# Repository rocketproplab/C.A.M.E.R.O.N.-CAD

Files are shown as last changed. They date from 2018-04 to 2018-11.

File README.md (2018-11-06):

# C.A.M.E.R.O.N

The main PCB on Launchy that is responsible for all the Avionics tasks of the rocket

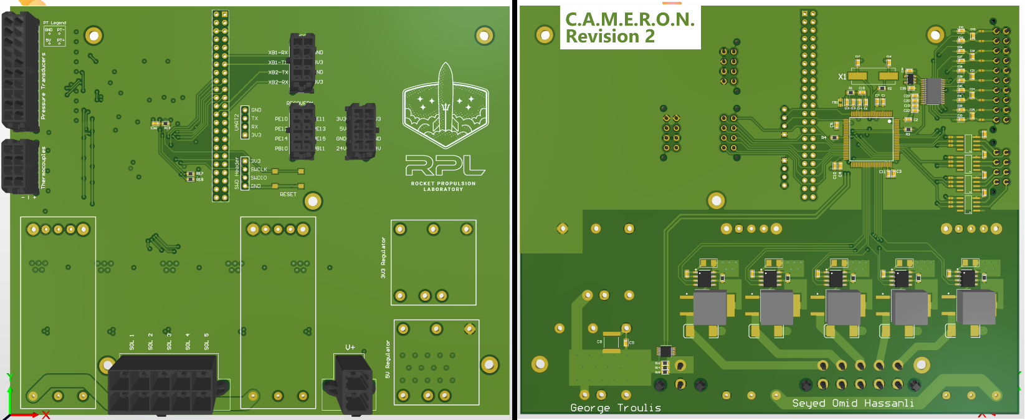
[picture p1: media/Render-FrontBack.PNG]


## Maintainer
CAMERON is maintained by George Troulis, with numerous contributions from Seyed Omid Hassanli

## Naming
C.A.M.E.R.O.N. stands for Changes All Mechanical and Electrical Requirements Over Night. It also happens to be the name of our beloved Chief Engineer, who has done a fantastic job at running RPL and assigning tasks and deadlines to everyone.

## Features

CAMERON contains the following features:
* Up to 36V input with 24V, 5V, and 3.3V rails
* Active current-monitoring IC connected to battery input
* BeagleBone Black (Flight Computer)
* Connector for 2 UARTs that connect the FC with XBee Radios
* STM32F4 "RIO" to interface with sensors
* Breakouts for Solenoids, Pressure Transducers, and Thermocouples
* SWD and UART Headers for debugging/programming the STM32F4
* Breakout for separate Recovery PCB that triggers chute at apogee

## Todo List for upcoming revisions
- [ ] Add indicator LEDs for various items
- [ ] Add designators to all components
- [ ] Shorten designators for multi-channel elements
- [X] Add Logo and Revision notes on the PCB
- [X] Fix footprint for solder bridge
- [X] Expand the diameter of the holes for the BeagleBone
- [X] Make annular rings for Molex connectors larger
- [X] FIX THE MOSFET FOOTPRINT (Gate and Drain are flipped)
- [X] Add thermal relief to pads
- [X] Add silk to the XBee connector and remove the J8 designator
- [X] FLIP BOOT PINS (test them first)
- [X] Move the "5V Regulator" Label away from the stitching vias
- [X] Add tenting to the stitching vias next to the power connector
- [X] Distribute silk designators on Generic GPIO breakout
- [X] Make copper pours reach the edges of the PCB
- [X] Add Silk designators to the TC/PT breakouts (PT1, TC1 etc)
- [X] Flip the flipped designators
- [X] Label 3V3 on the SWD Header
- [ ] ~~Add Reset signal to Programming header~~ (Not necessary)

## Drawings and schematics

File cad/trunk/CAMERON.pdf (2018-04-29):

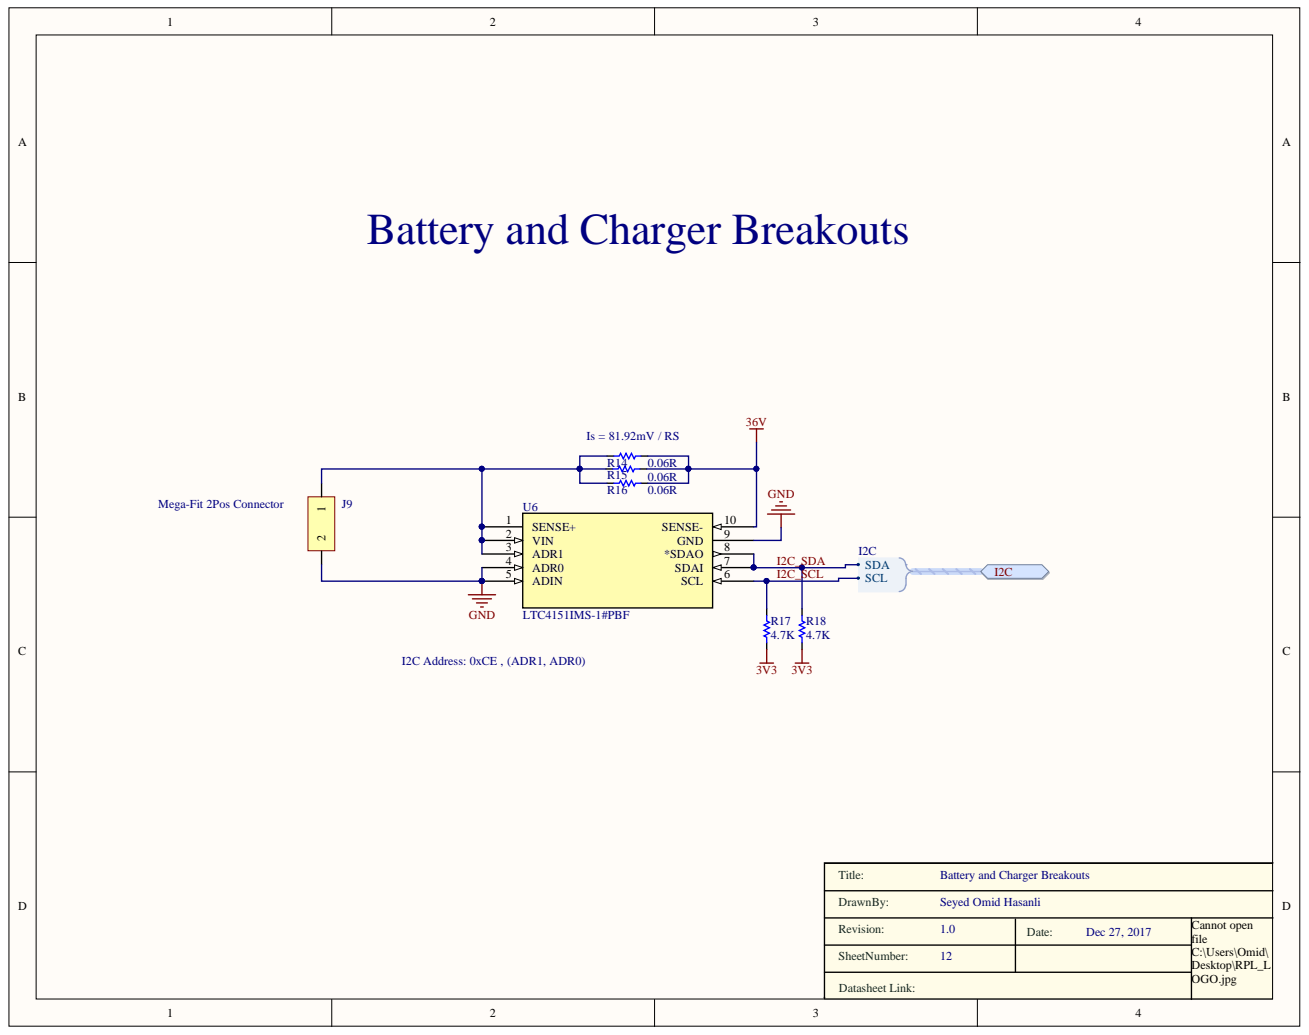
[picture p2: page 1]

Revi s ion: 1. 0 | D a t e : D e c 27, 2017 | Cannot open fi l e C: \ U s ers \ O m id\ D e sktop\RP L_L O G O . jpg

She e tNumber:

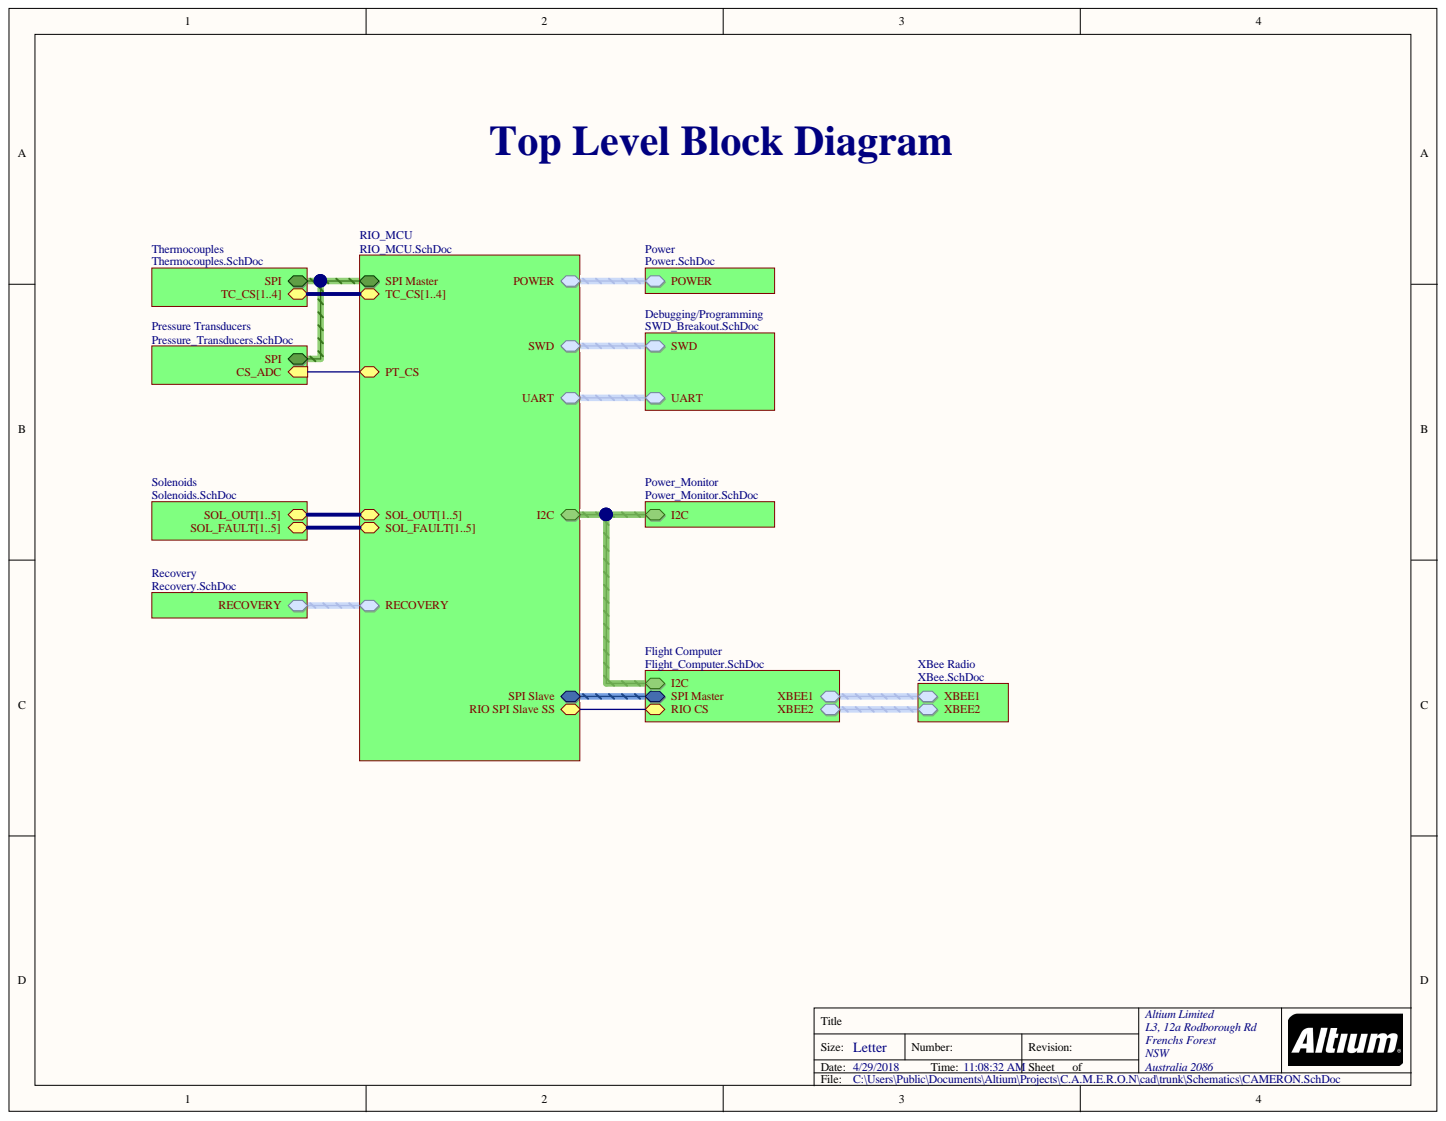
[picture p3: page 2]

Top Level Block Diagram

RIO SPI Slave SS

Title | Altium Limited L3, 12a Rodborough Rd Frenchs Forest NSW Australia 2086

Letter Size: | Number: | Revision:
Date: 4/29/2018 Time: 11:08:32 AM | | Sheet of

C:\Users\Public\Documents\Altium\Projects\C.A.M.E.R.O.N\cad\trunk\Schematics\CAMERON.SchDoc

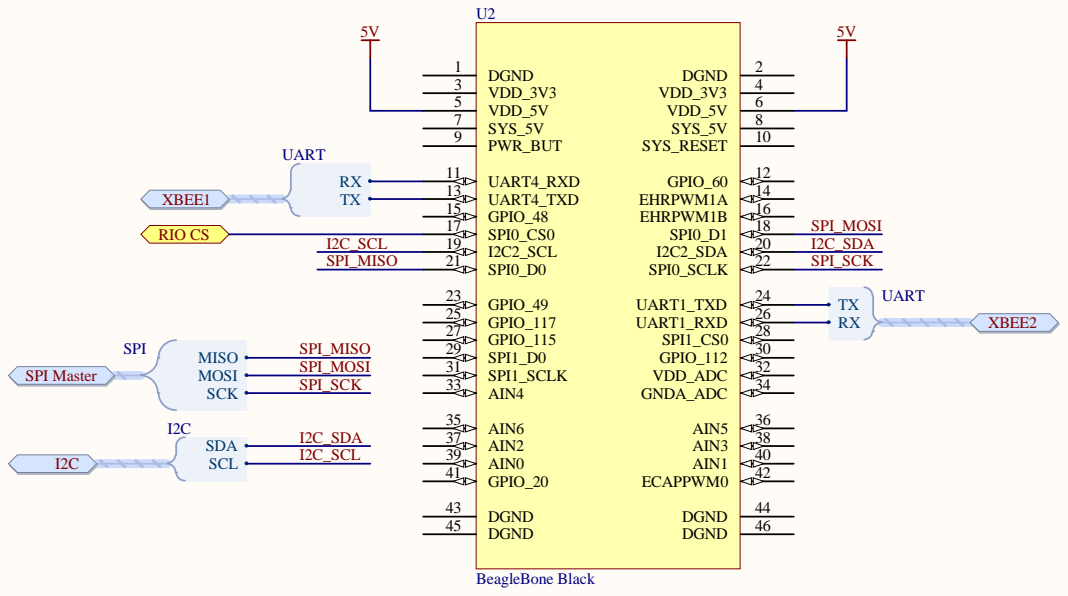
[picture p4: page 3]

C:\Users\Public\Documents\Altium\Projects\C.A.M.E.R.O.N\cad\trunk\Schematics\MCU\Flight_Computer.SchDoc

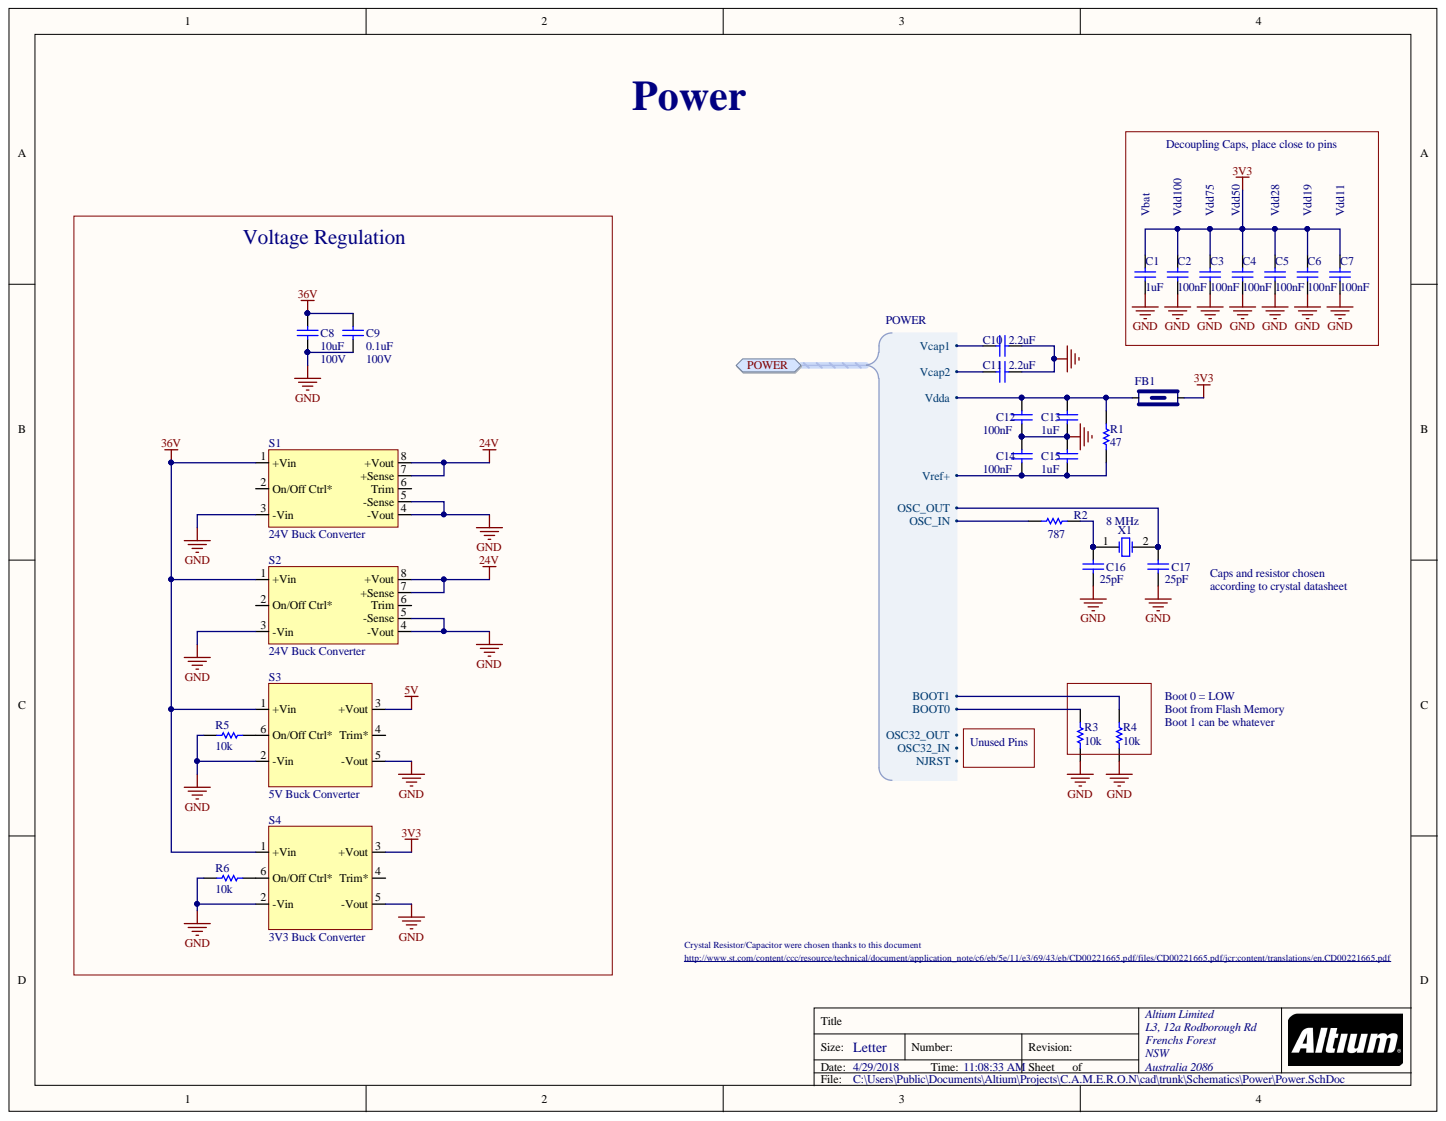
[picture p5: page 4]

Deco u p l i n g Cap 3 V | s, p lace cl o se t o p i n s 3 D

T i tl e | A l t i u m Li m i ted L3, 1 a R o db o ro u g h R d French s Fo res NS W A u ra l i a 2

Size: | N umber: | Rev i i o n :

/ / T ime: : : 3 A M | | Sheet o f

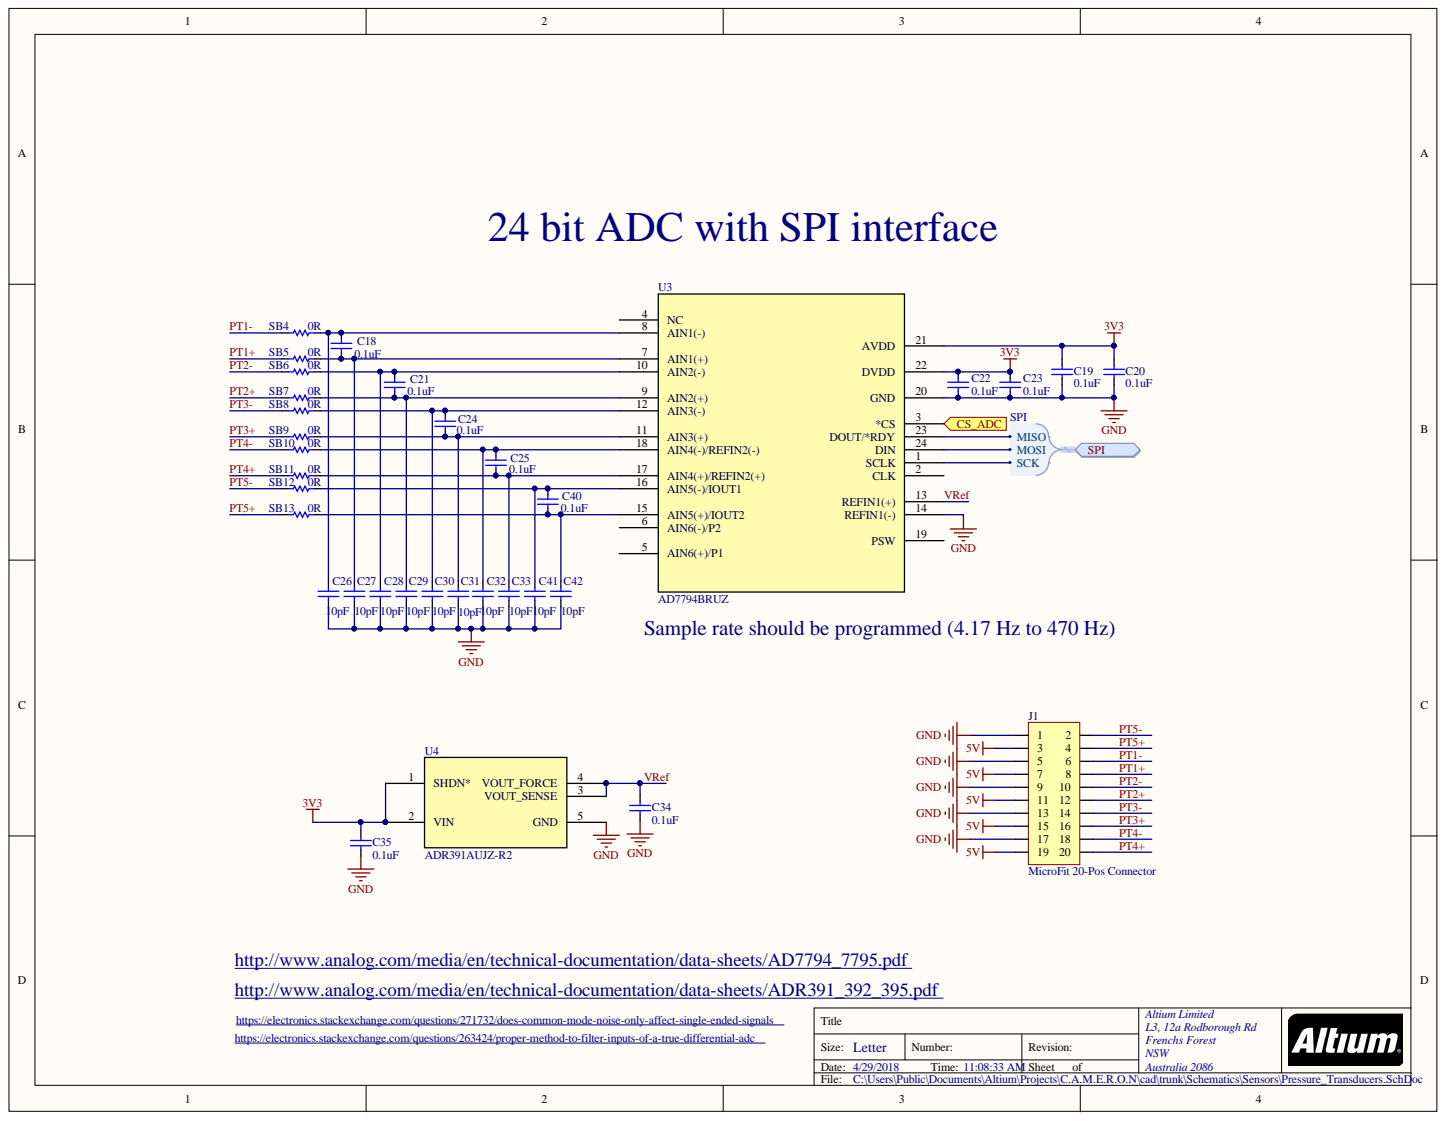
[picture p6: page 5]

24 bit ADC with SPI interface

AIN2(-) 10

C21 0.1uF | AIN2(+) 9

AIN3(-) 12

C24 0.1uF | AIN3(+) 11

AIN4(-)/REFIN2(-) 18

0.1uF C25 | AIN4(+)/REFIN2(+) 17

AIN5(-)/IOUT1 16

C40 | AIN5(+)/IOUT2 15

AIN6(-)/P2 6 AIN6(+)/P1 5

AD7794BRUZ
Sample rate should be programmed (4.17 Hz to 470 Hz)

http://www.analog.com/media/en/technical-documentation/data-sheets/AD7794_7795.pdf
http://www.analog.com/media/en/technical-documentation/data-sheets/ADR391_392_395.pdf

https://electronics.stackexchange.com/questions/271732/does-common-mode-noise-only-affect-single-ended-signals
https://electronics.stackexchange.com/questions/263424/proper-method-to-filter-inputs-of-a-true-differential-adc

C:\Users\Public\Documents\Altium\Projects\C.A.M.E.R.O.N\cad\trunk\Schematics\Sensors\Pressure_Transducers.SchDoc

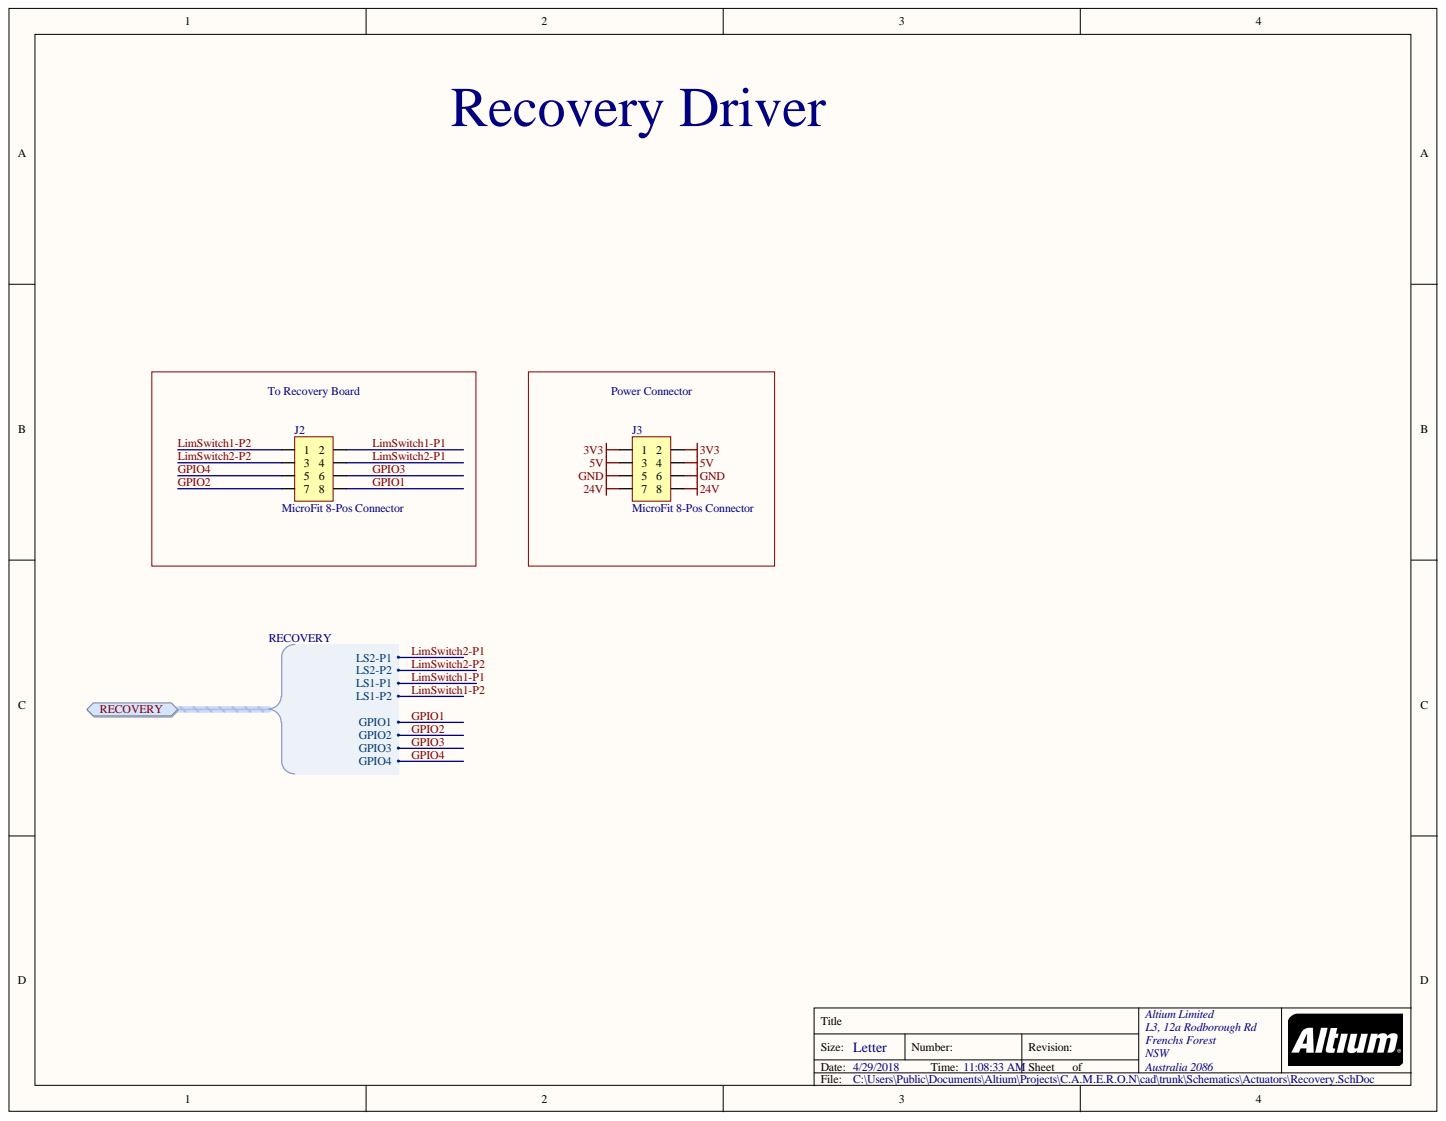
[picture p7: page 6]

C:\Users\Public\Documents\Altium\Projects\C.A.M.E.R.O.N\cad\trunk\Schematics\Actuators\Recovery.SchDoc

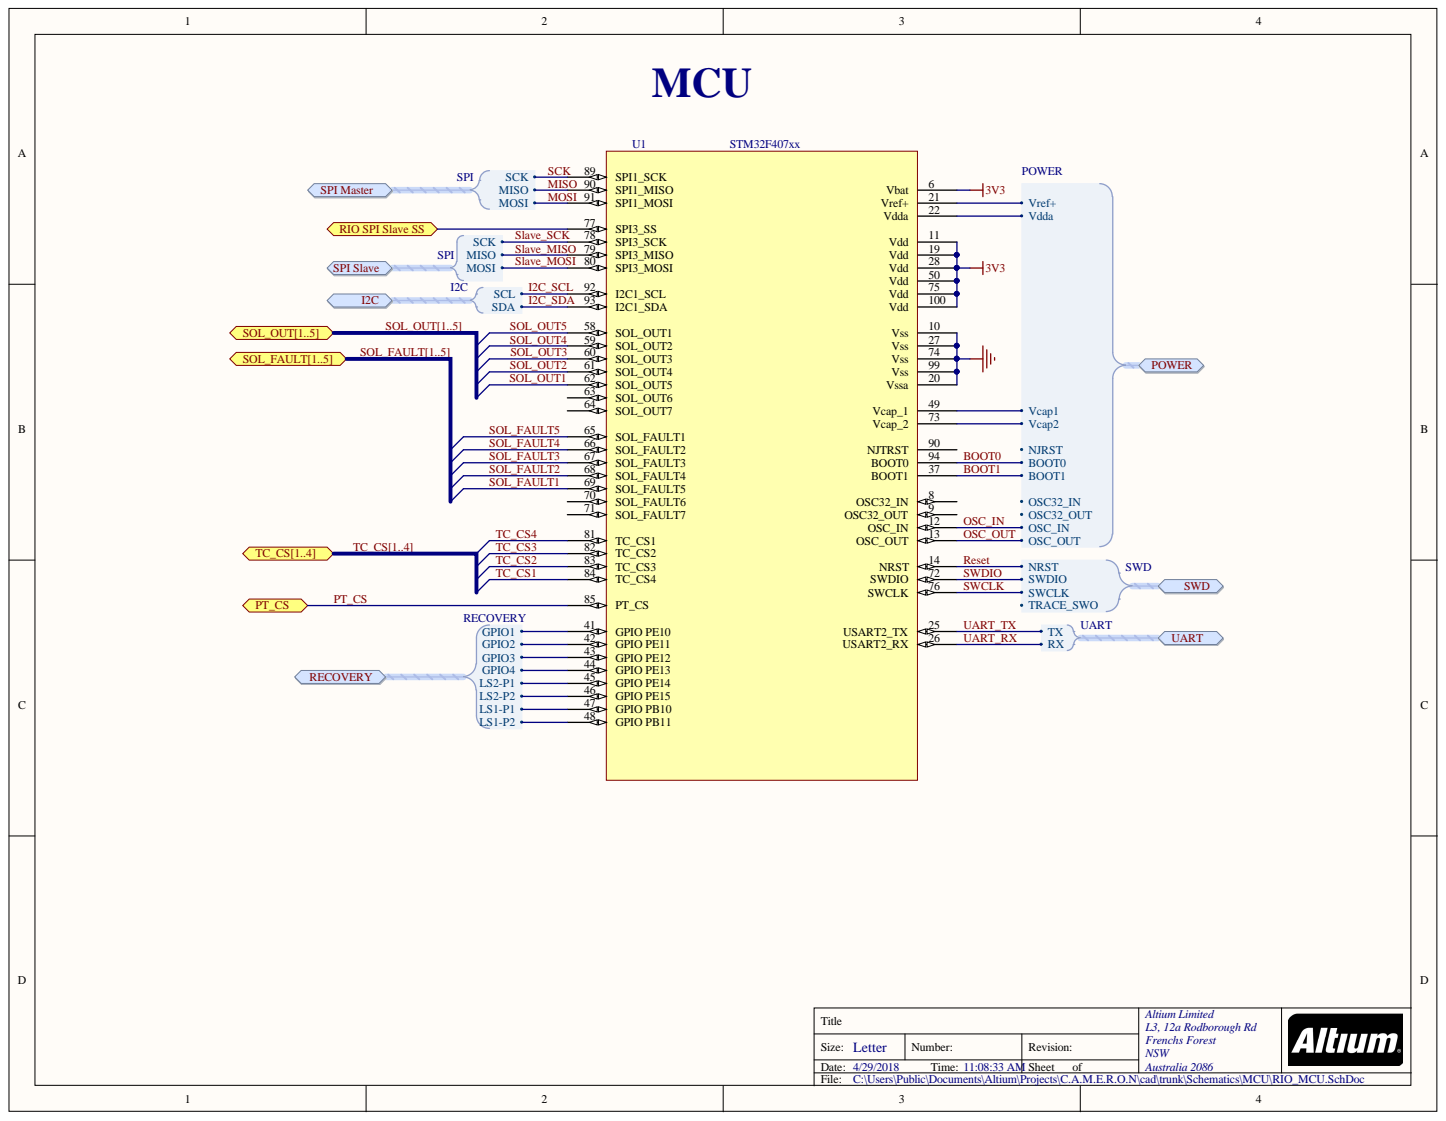
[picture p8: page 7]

RIO SPI Slave SS

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

Size: | N umber: | Rev i i o n :

/ / T ime: : : 3 A M | | Sheet o f

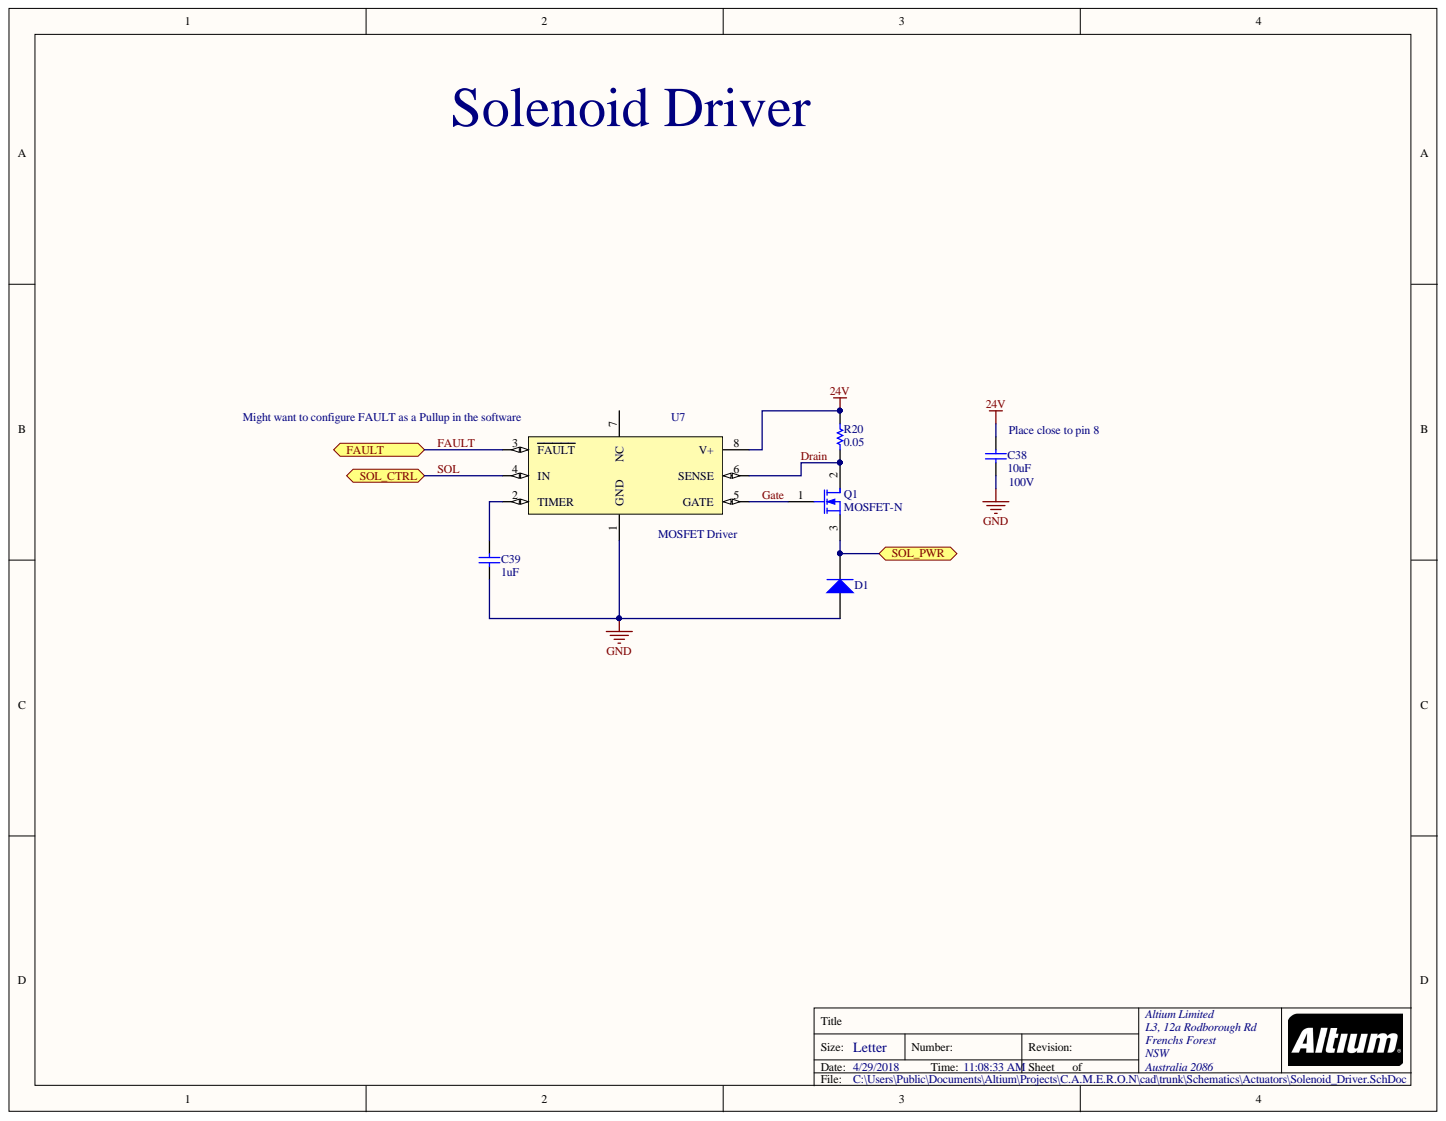
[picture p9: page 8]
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

Size: | N umber: | Rev i i o n :

/ / T ime: : : 3 A M | | Sheet o f

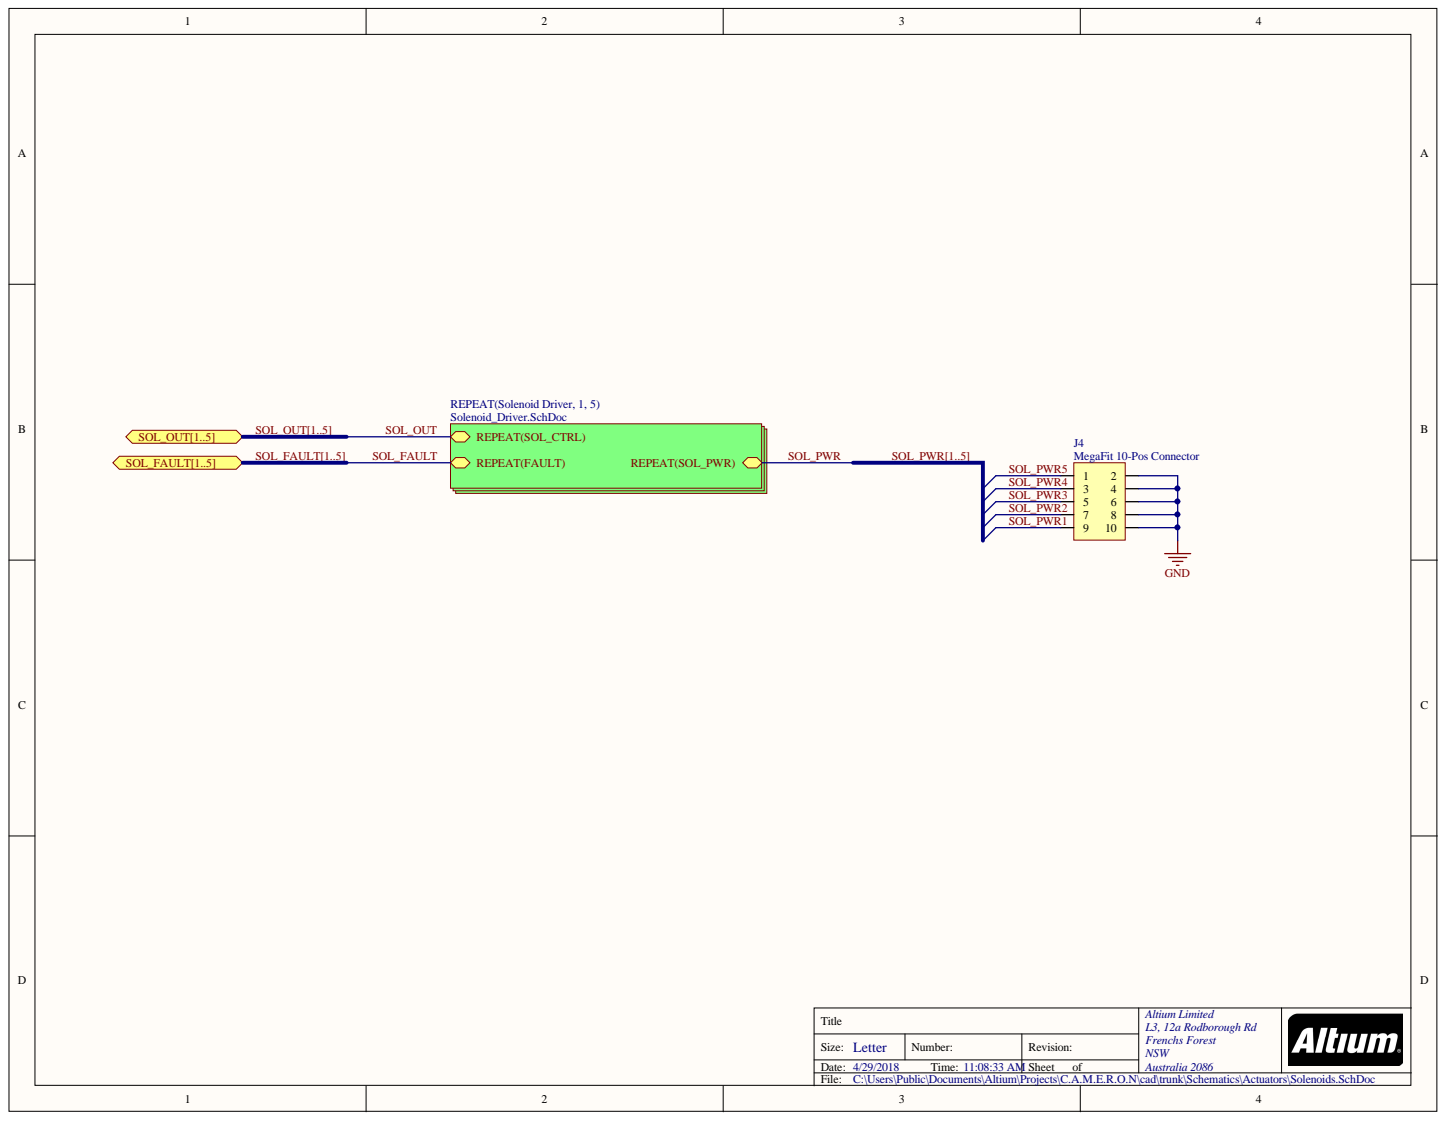
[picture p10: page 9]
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

Size: | N umber: | Rev i i o n :

/ / T ime: : : 3 A M | | Sheet o f

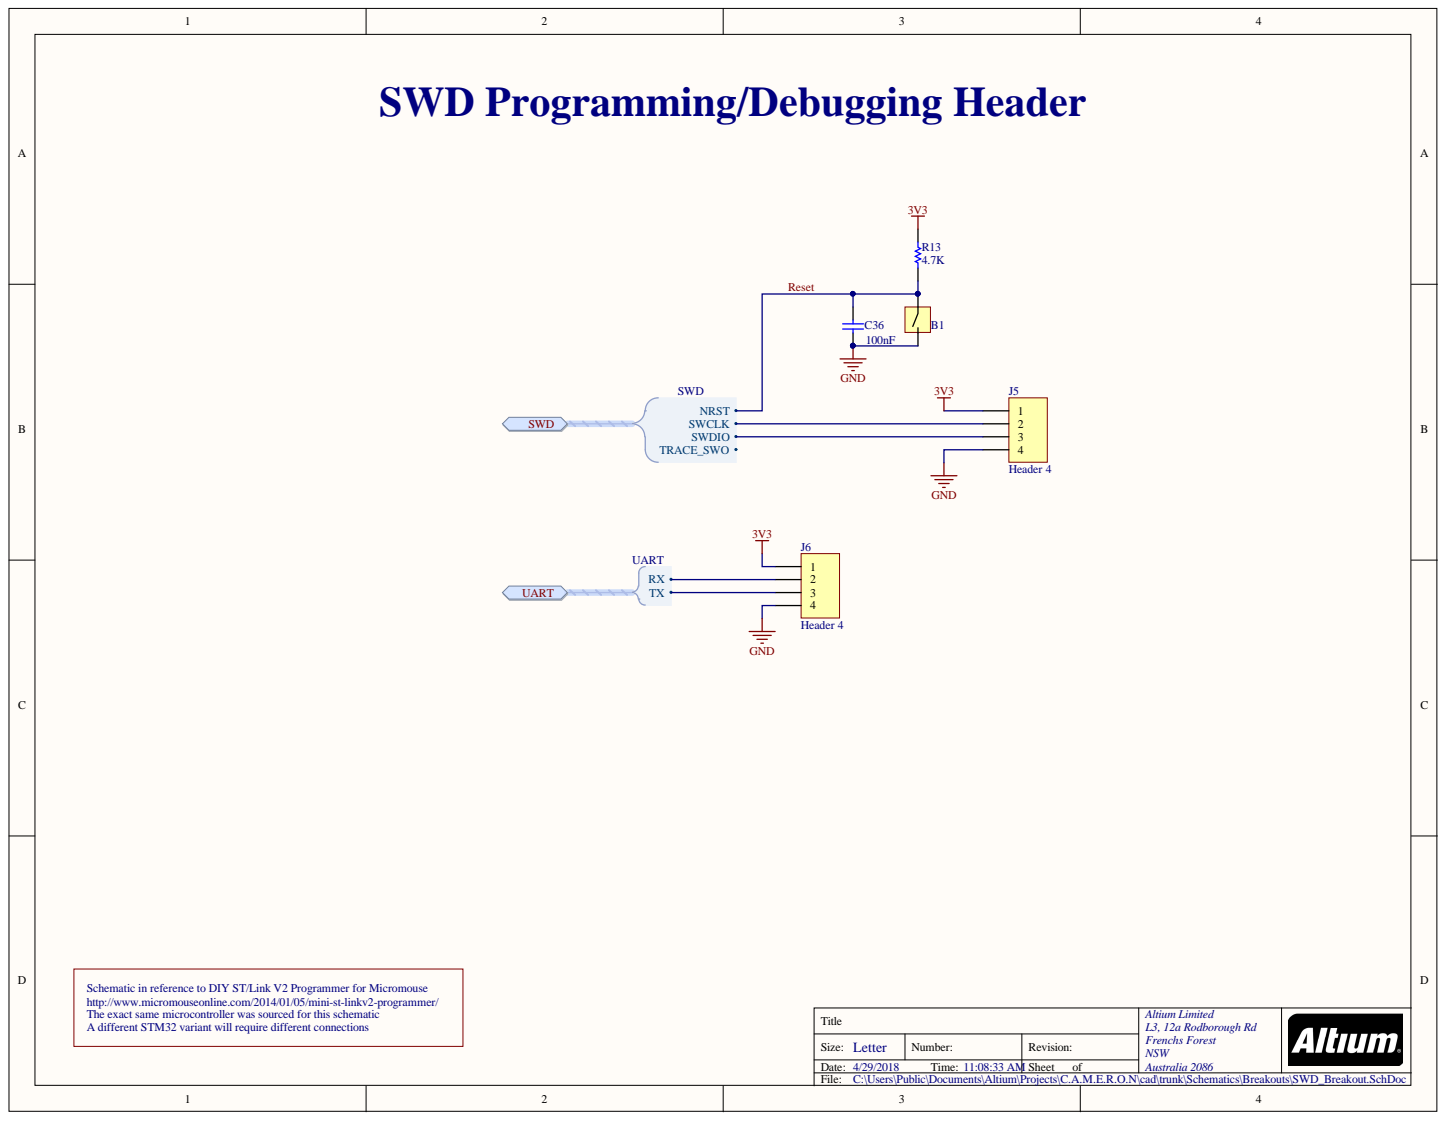
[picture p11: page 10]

SWD Programming/Debugging Header

Schematic in reference to DIY ST/Link V2 Programmer for Micromouse
http://www.micromouseonline.com/2014/01/05/mini-st-linkv2-programmer/
The exact same microcontroller was sourced for this schematic
A different STM32 variant will require different connections

C:\Users\Public\Documents\Altium\Projects\C.A.M.E.R.O.N\cad\trunk\Schematics\Breakouts\SWD_Breakout.SchDoc

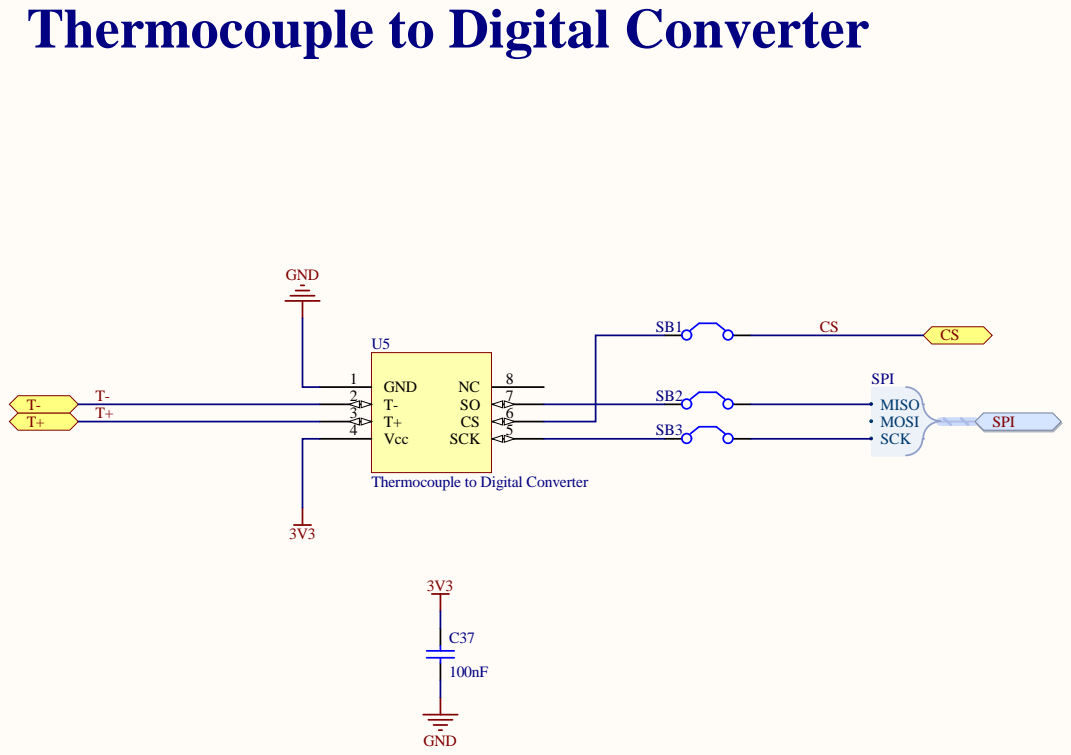
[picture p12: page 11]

Thermocouple to Digital Converter

C:\Users\Public\Documents\Altium\Projects\C.A.M.E.R.O.N\cad\trunk\Schematics\Sensors\Thermocouple_Amplifier.SchDoc

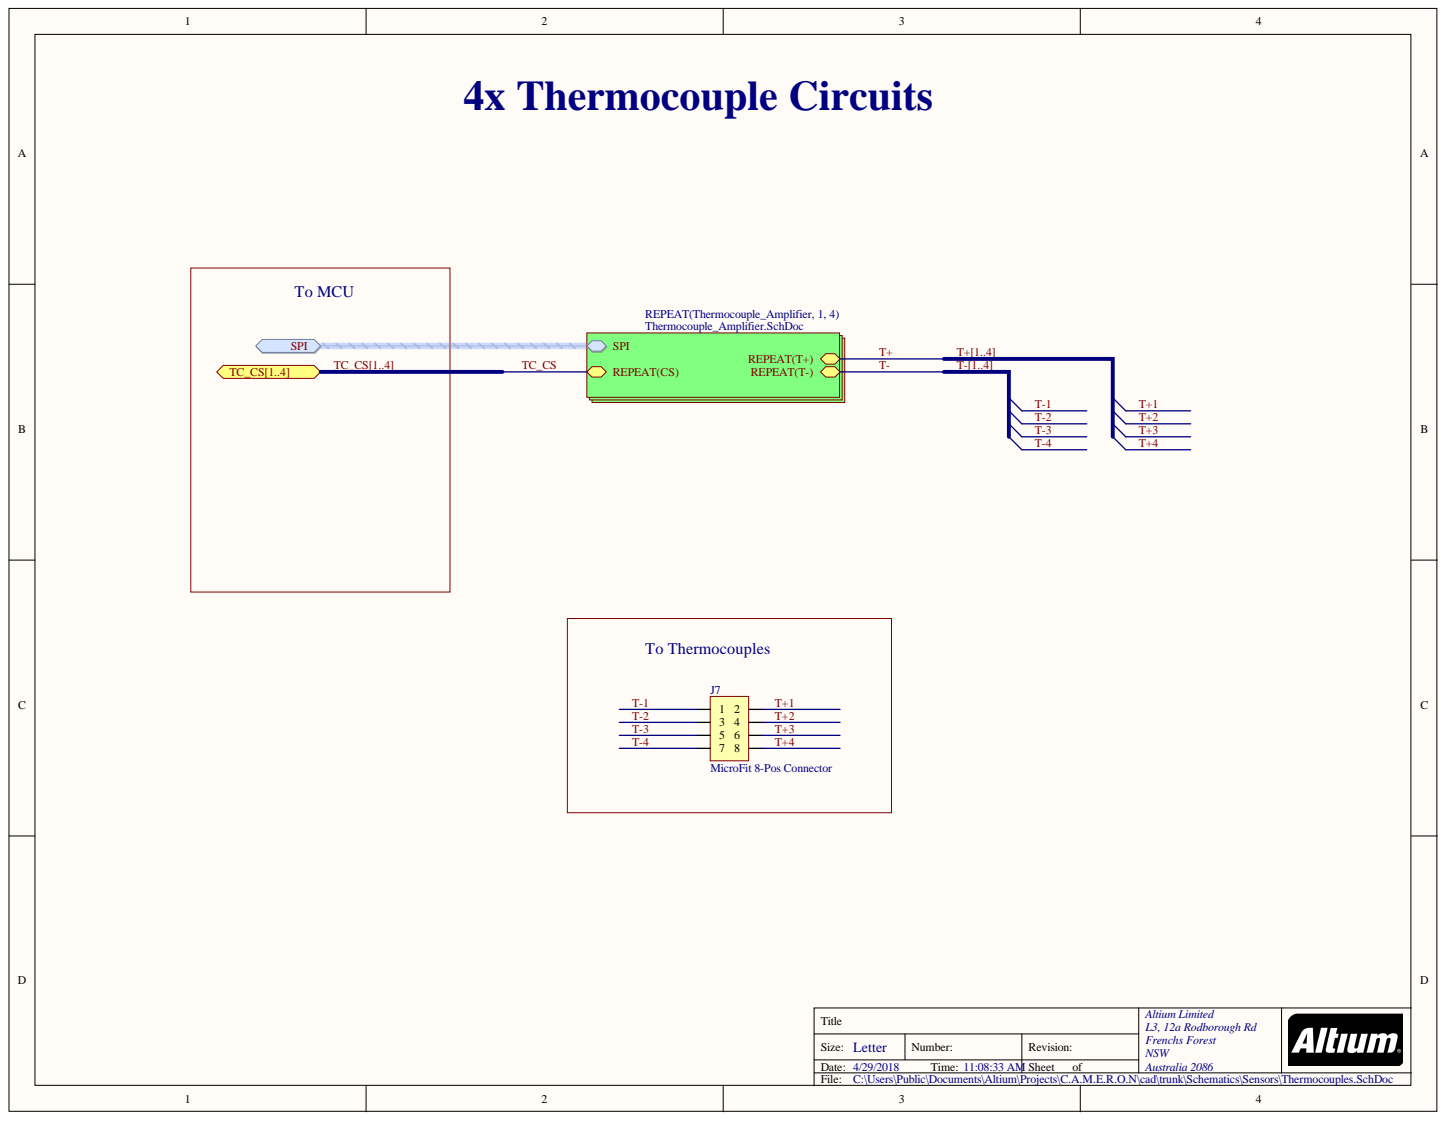
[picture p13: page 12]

C:\Users\Public\Documents\Altium\Projects\C.A.M.E.R.O.N\cad\trunk\Schematics\Sensors\Thermocouples.SchDoc

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

Size: | N umber: | Rev i i o n :

/ / T ime: : : 3 A M | | Sheet o f


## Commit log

2018-01-28 Initial commit, RIO Files only TODO Merge Omid's Power Distribution board
    [ADC_GPIO_Breakout.SchDoc, CAMERON.PcbDoc, CAMERON.PrjPcb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]
2018-01-29 Cleaned up unnecessary files, renaming, and preliminary PCB Shape
    [ADC_GPIO_Breakout.SchDoc, CAMERON.PcbDoc, CAMERON.PrjPcb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]
2018-02-03 Re-structured file locations and updated top-level diagram
    [CAMERON.PrjPcb, CAMERON.SchDoc, Flight_Computer.SchDoc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]
2018-02-06 PT
    Pressure Transducers Schematics Update (Footprint Updated)
    [Pressure_Transducers.SchDoc]
2018-02-06 Added more top-level schematics and library parts
    [CAMERON.PcbDoc, CAMERON.PrjPcb, CAMERON.SchDoc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]
2018-02-06 Power Monitor
    Power Monitor and required Footprints added to the CAMERON
    [CAMERON.PrjPcb, Power_Monitor.SchDoc]
2018-02-06 Input Voltage Correction
    Changing the PT's Input voltages from 10Vdc to 5Vdc and In Power monitor changing +3V3 to 3V3 global lable used by my buddy
    [Power_Monitor.SchDoc, Pressure_Transducers.SchDoc]
2018-02-07 Initial schematic mostly finished, first compilation
    [CAMERON.PrjPcb, CAMERON.SchDoc, CAN_Breakout.SchDoc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]
2018-02-07 Footprint and schematic updates
    [CAMERON.PrjPcb, CAMERON.SchDoc, Flight_Computer.SchDoc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]
2018-02-08 Xbee Schematic and Footprint Update
    Footprint library
2018-02-08 Started PCB Routing
    [CAMERON.PcbDoc, CAMERON.PrjPcb, CAMERON.SchDoc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]
2018-02-08 24V 3A DC-DC Converter
    24V 3A DC-DC Converter Footprint And Schematic Symbol Added
2018-02-09 Following Schematics and Footprints added to library
    SPM15-033-Q48N-C
    SPM15-050-Q12P-C
    UVQ-24/4.5-D24PB-C
    CONV DC/DC 72W 24V 3A
2018-02-10 routed Solenoids, TC, and PT sensors
    [CAMERON.PcbDoc, CAMERON.PrjPcb, CAMERON.SchDoc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]
2018-02-12 Continuation of routing, started adding Power regulators
    [CAMERON.PcbDoc, CAMERON.PrjPcb, Power.SchDoc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]
2018-02-14 Added Molex Connectors and continued routing
    [CAMERON.PcbDoc, CAMERON.PrjPcb, Power.SchDoc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]
2018-02-14 Main Power Connections
    DC-DC convertors connection to the main board
    [Power.SchDoc, Power_Monitor.SchDoc]
2018-02-16 IMU, Raven, Solenoids and Symbols/Footprint
    Rven Schematics and Foot print Added.
    Pressure, Gyro, Accerometer, Temp, Humid Sensor added.
    Voltage for Solenoid Fault pin Reviewed and still needs to be finilized
    [IMU.SchDoc, Raven.SchDoc, Solenoid_Driver.SchDoc]
2018-02-16 Raven Footprint Edit
    [IMU.SchDoc]
2018-02-20 Significant size/price reduction, routing 90% done
    [CAMERON.PcbDoc, CAMERON.PrjPcb, CAMERON.SchDoc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]
2018-02-21 Almost finished routing, added UART Breakout
    [CAMERON.PcbDoc, CAMERON.PrjPcb, CAMERON.SchDoc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]
2018-02-25 Added recovery breakouts, silkskreen, and final routing
    [CAMERON.PcbDoc, CAMERON.PrjPcb, CAMERON.SchDoc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]
2018-02-25 Added polygon pours to top/bottom layers
    [CAMERON.PcbDoc]
2018-02-25 Minor DRC changes for Advanced Circuits Fabrication
    [CAMERON.PcbDoc, CAMERON.PrjPcb]
2018-02-26 Final violations fix, and added some stitching vias
    [CAMERON.PcbDoc, CAMERON.PrjPcb]
2018-02-26 Added schematics to tag1 and sent files for fabrication
    [CAMERON.PcbDoc, CAMERON.PrjPcb, CAMERON.SchDoc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]
2018-03-24 Added TODO list in README for newer revisions of CAMERON Implemented some features from the TODO list Added some 3D models
    [CAMERON.PcbDoc, RIO_MCU.SchDoc, XBee.SchDoc]
2018-04-23 Fixed many of the items on the TODO List, and added logo files
    [CAMERON.PcbDoc, CAMERON.PrjPcb, Power.SchDoc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]
2018-04-27 Finished routing rev2, ready for manufacture
    [CAMERON.PcbDoc, CAMERON.PrjPcb, Power.SchDoc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]
2018-04-28 Final tweaks, and submitted for fabrication
    [CAMERON.PcbDoc, CAMERON.PrjPcb, Power.SchDoc]
2018-04-28 Tagged rev2
    [CAMERON.PcbDoc, CAMERON.PrjPcb, CAMERON.SchDoc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]
